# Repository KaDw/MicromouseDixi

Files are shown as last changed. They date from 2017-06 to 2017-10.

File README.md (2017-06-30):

# Micromouse Dixi #
	
|  |  |
| ----- | ----- |
| Width | 79mm  |
| Length  | 95mm  |
| Weight  | |
| Wheels  | 3D printed wheels + MZT301-20 tyres  |
| Microcontroller  | STM32F405RGT6  |
| Gear ratio  | 27:42  |
| Motor  | Pololu 5:1 HPCB  |
| Encoders  | AS55147P  |
| Battery  | Li-Pol Dualsky 7.4V 150mAh 20C  |
| Motor Driver  | TB6612FNG  |
| Sensor | TEFT4300 + SFH4545 X 6  |
| Gyro | MPU6050  |

[BOM](https://docs.google.com/spreadsheets/d/1-OBliDhJaHepW5BqGZAOIfc_tJH4ITr39Bejxq-Zry4/edit?usp=sharing)

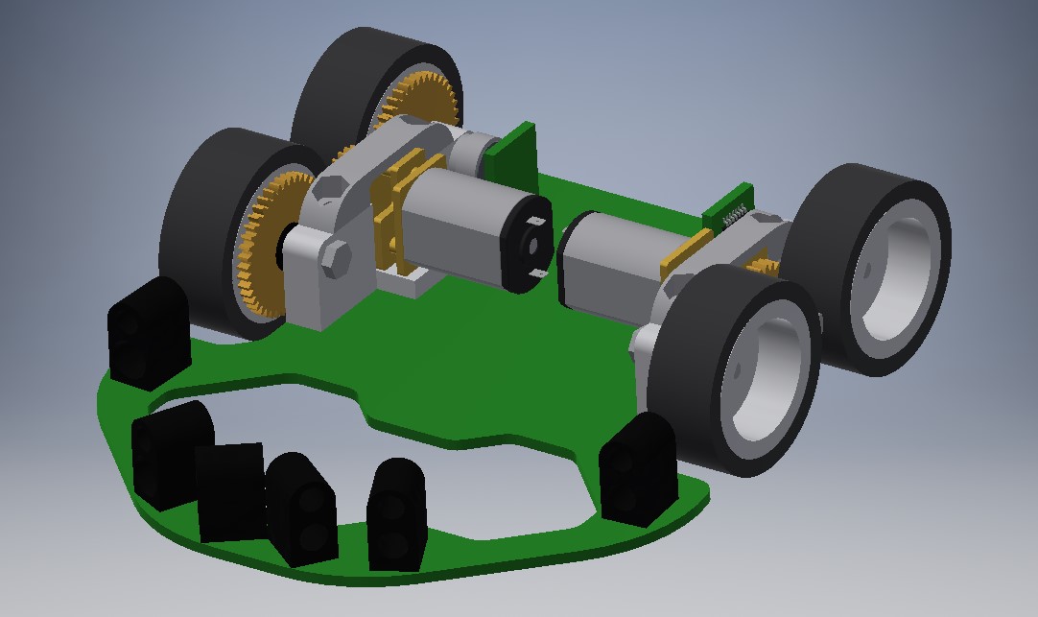
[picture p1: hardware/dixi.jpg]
Dixi


### Development tools ###

* STM32CubeMX Version 4.17.0
* HAL Libraries - FW_F4 V1.13.1
* Keil uVision 5.21a
* EagleCAD 7.7
* Autodesk Inventor 2016

Development tools available [here](https://drive.google.com/open?id=0B6SlddUSFtelRTBFR0EwWk1qT1k)

### Setup ###

* CubeMX setup
You can get HAL libraries by going to Help->Install New Libraries->Firmware Package for Family STM32F4.
...

### Who do I talk to? ###

* Karol Trzciński k.trzcinski95@gmail.com
* Karol Dworakowski karol1dw@gmail.com

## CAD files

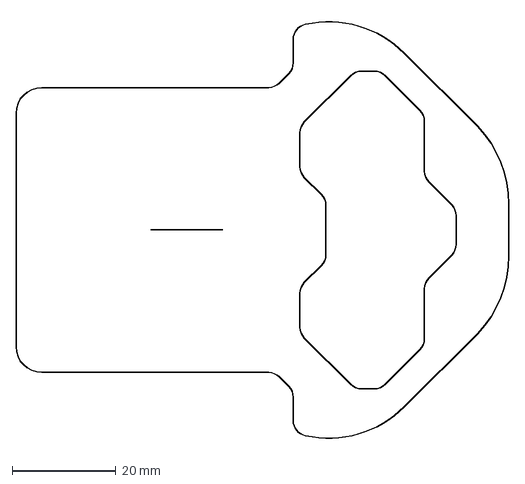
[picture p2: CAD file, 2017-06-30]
hardware/models/mainpcb.dxf
95.2 x 82.5 mm

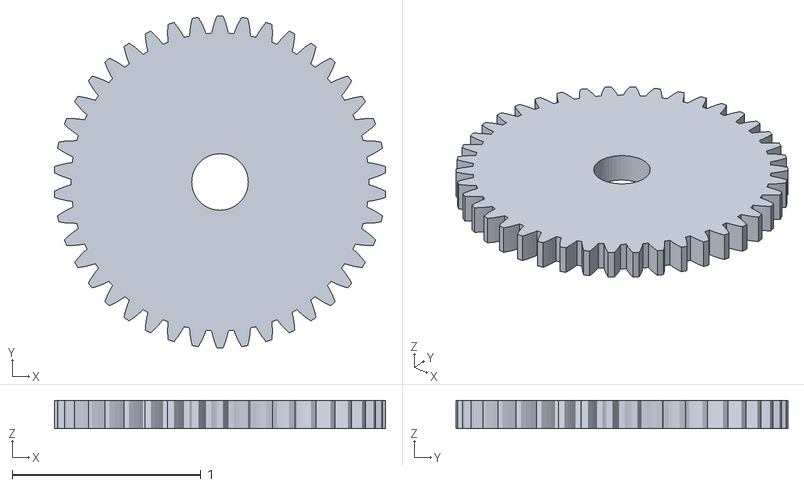
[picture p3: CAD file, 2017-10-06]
hardware/models/gear_42t.stl
1.76 x 1.76 x 0.15

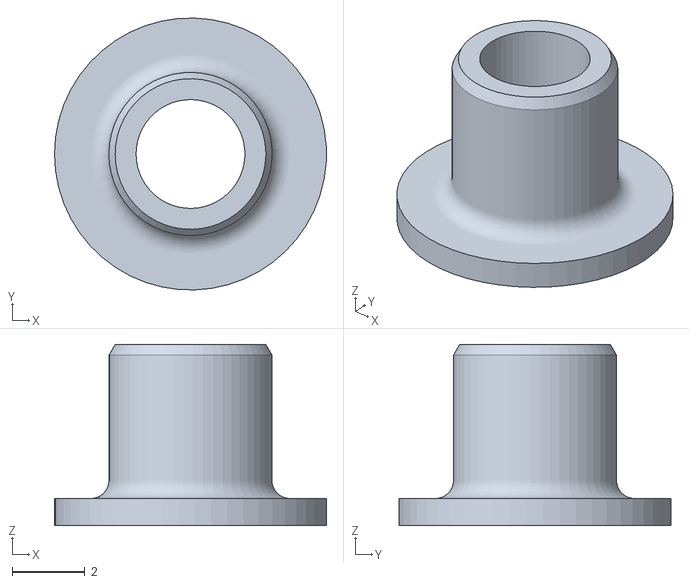
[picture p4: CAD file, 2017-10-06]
hardware/models/XFM_0304_05_2.stl
7.50 x 7.50 x 5.00

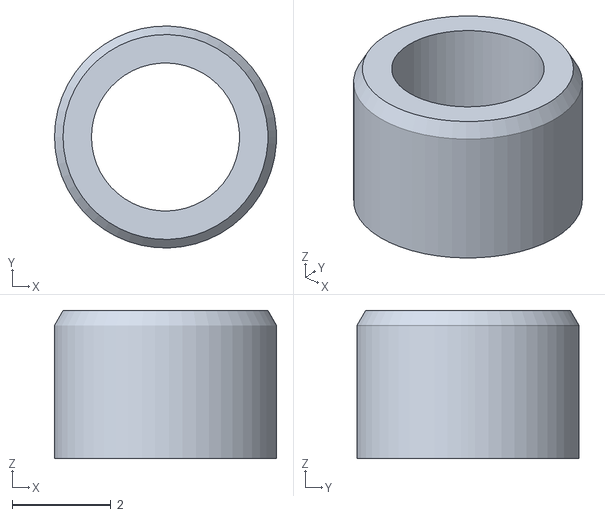
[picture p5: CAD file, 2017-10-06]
hardware/models/XSM_0304_03_1.stl
4.50 x 4.50 x 3.00

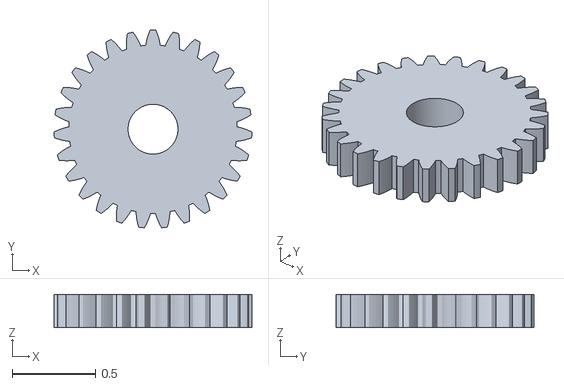
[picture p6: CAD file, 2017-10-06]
hardware/models/gear_27t.stl
1.19 x 1.19 x 0.2

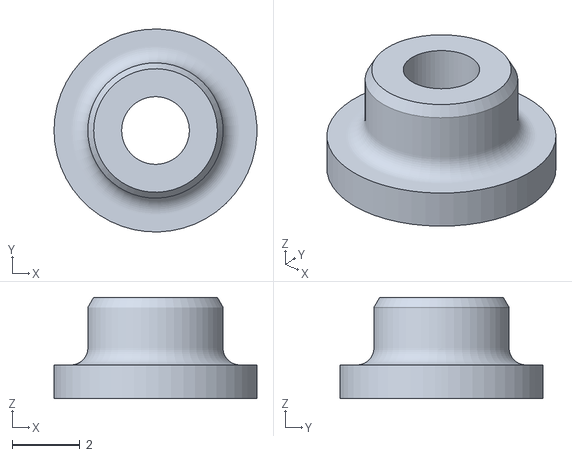
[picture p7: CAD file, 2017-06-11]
hardware/models/XFM_020406_03_2.stl
6.00 x 6.00 x 3.00

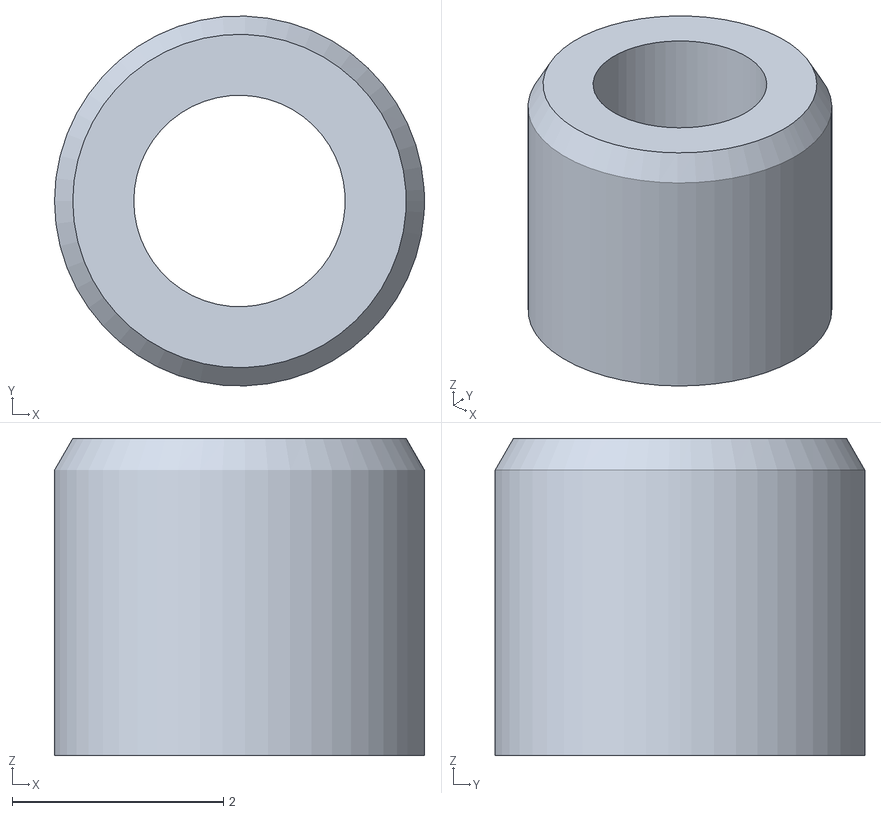
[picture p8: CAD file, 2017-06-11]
hardware/models/XSM_0203_03_1.stl
3.50 x 3.50 x 3.00

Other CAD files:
hardware/models/Dixi.iam
hardware/models/Dixi/Design Accelerator/Spur Gear14.ipt
hardware/models/Dixi/Design Accelerator/Spur Gear23.ipt
hardware/models/Dixi/Design Accelerator/Spur Gears3.iam
hardware/models/Dixi/Design Accelerator/Spur Gears4.iam
hardware/models/XFM_020406_03_233.ipt
hardware/models/XSM_0203_03_1.ipt
hardware/models/bolt.ipt
hardware/models/enc_pcb.ipt
hardware/models/koloz.ipt
hardware/models/led_mount.ipt
hardware/models/magnet.ipt
hardware/models/magnet_holder.ipt
hardware/models/mainpcb.ipt
hardware/models/motor.ipt
hardware/models/togh.ipt
hardware/models/togh_MIR5.ipt
hardware/models/top_mount.ipt
hardware/models/tssop14.iam
hardware/models/tssop14_1.ipt
hardware/models/tssop14_2.ipt
hardware/models/tssop14_3.ipt
hardware/models/tyre.ipt
hardware/models/wheel.ipt

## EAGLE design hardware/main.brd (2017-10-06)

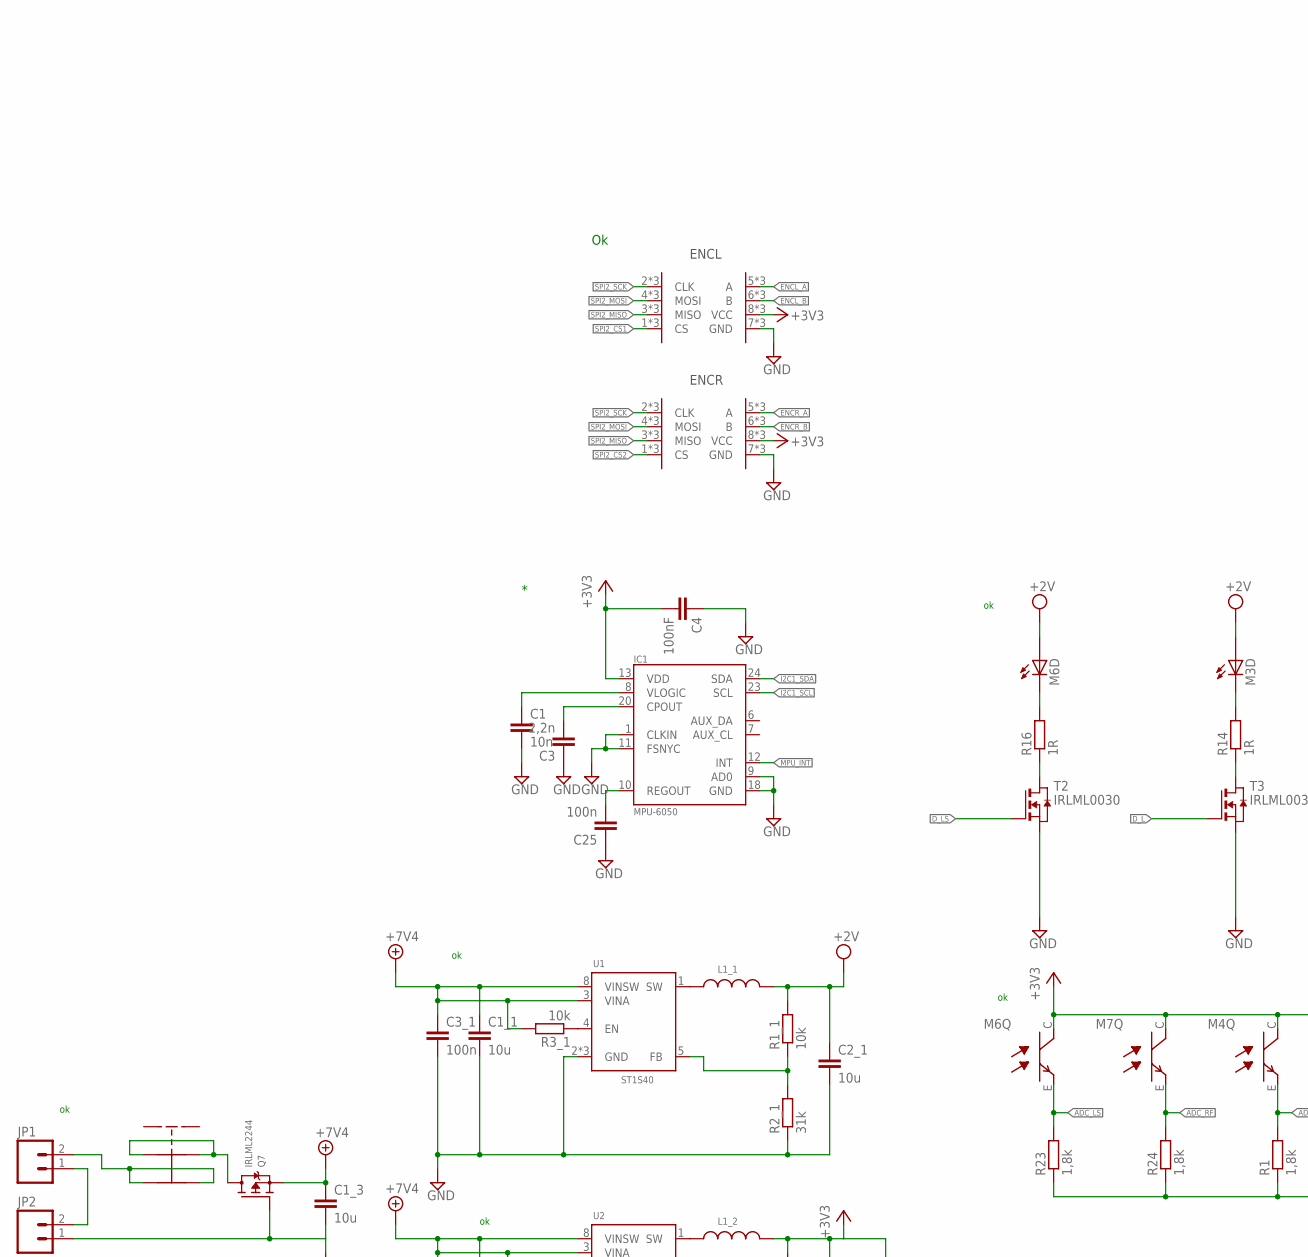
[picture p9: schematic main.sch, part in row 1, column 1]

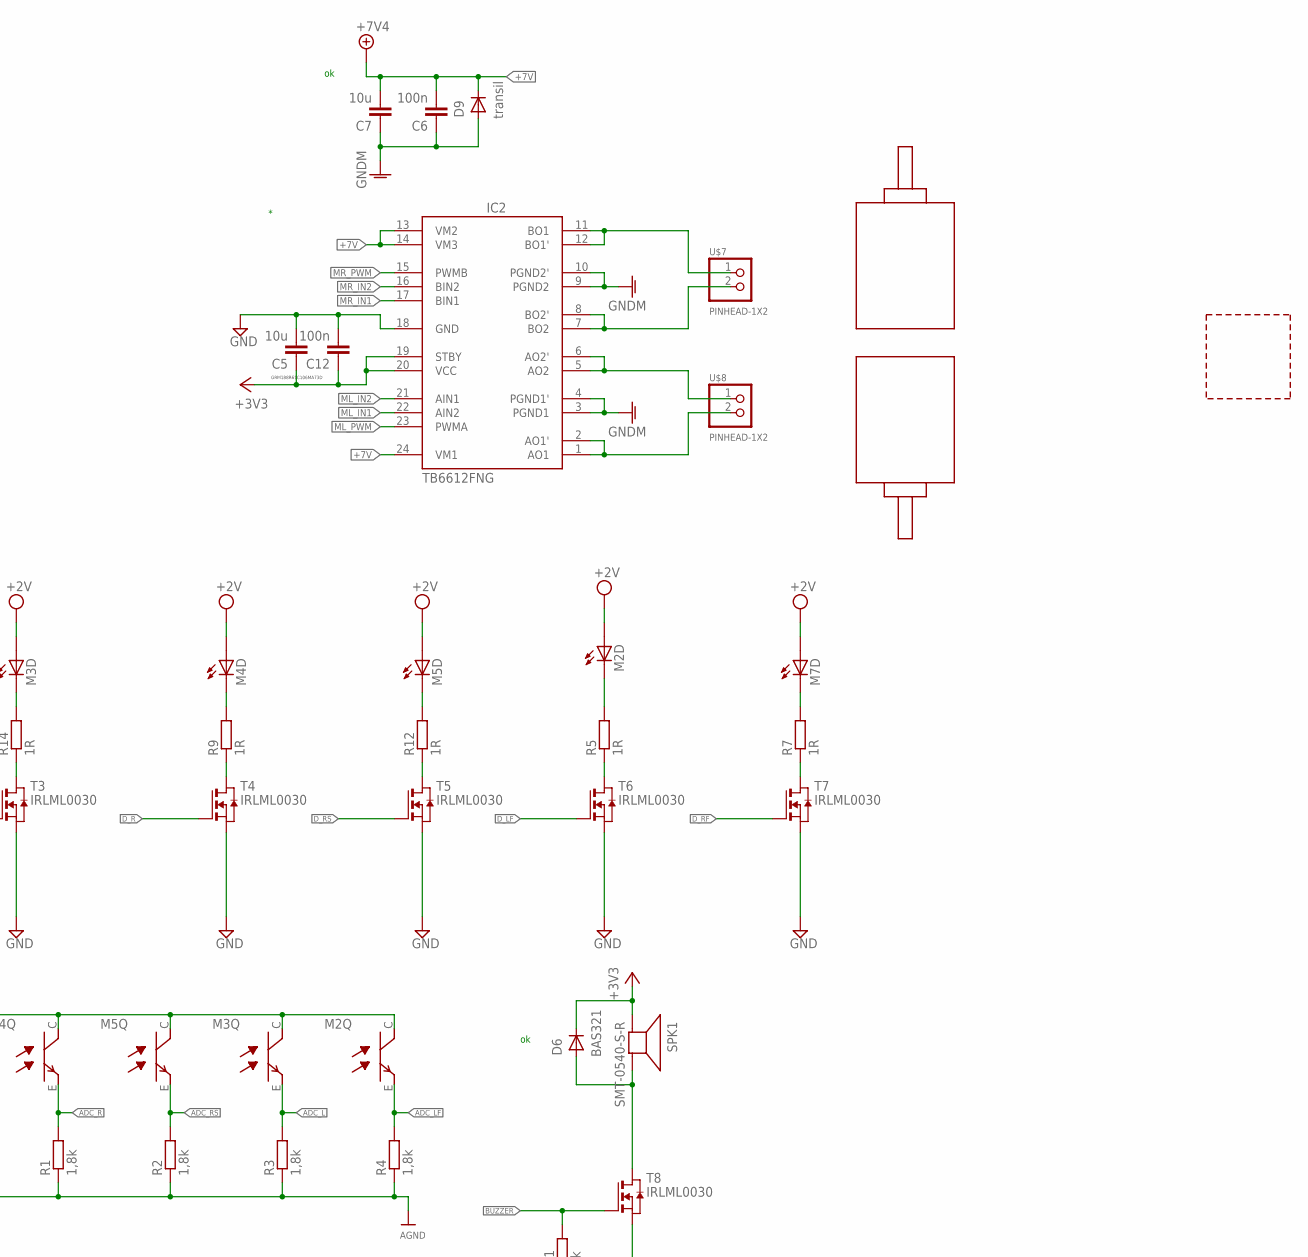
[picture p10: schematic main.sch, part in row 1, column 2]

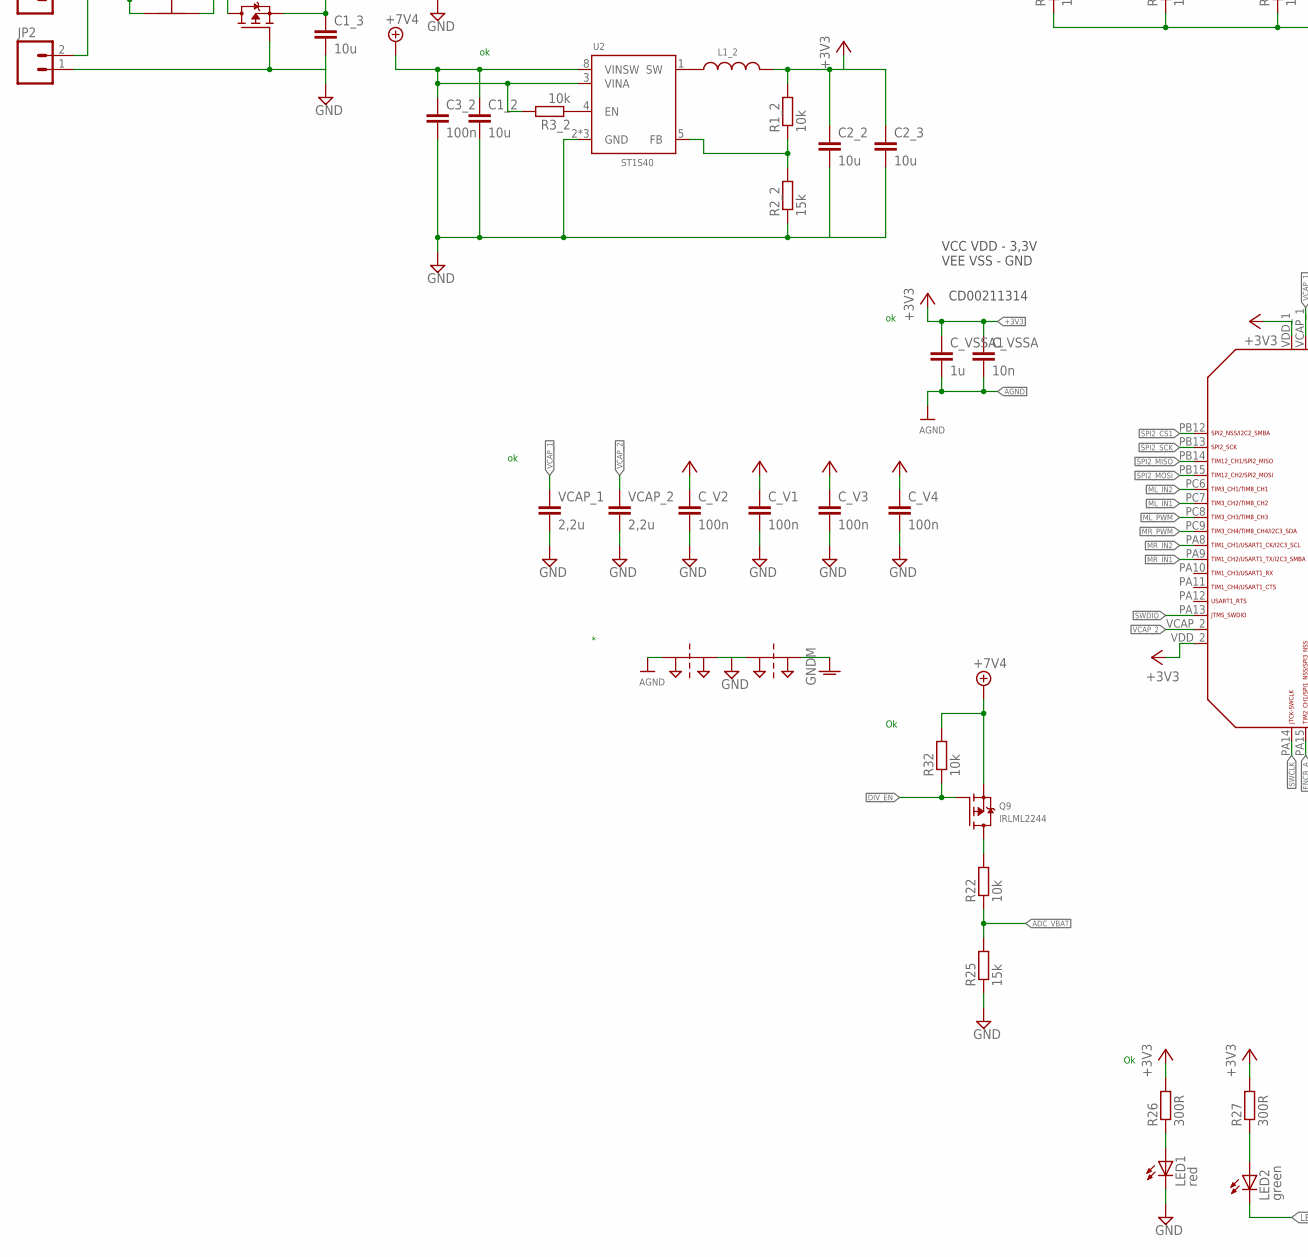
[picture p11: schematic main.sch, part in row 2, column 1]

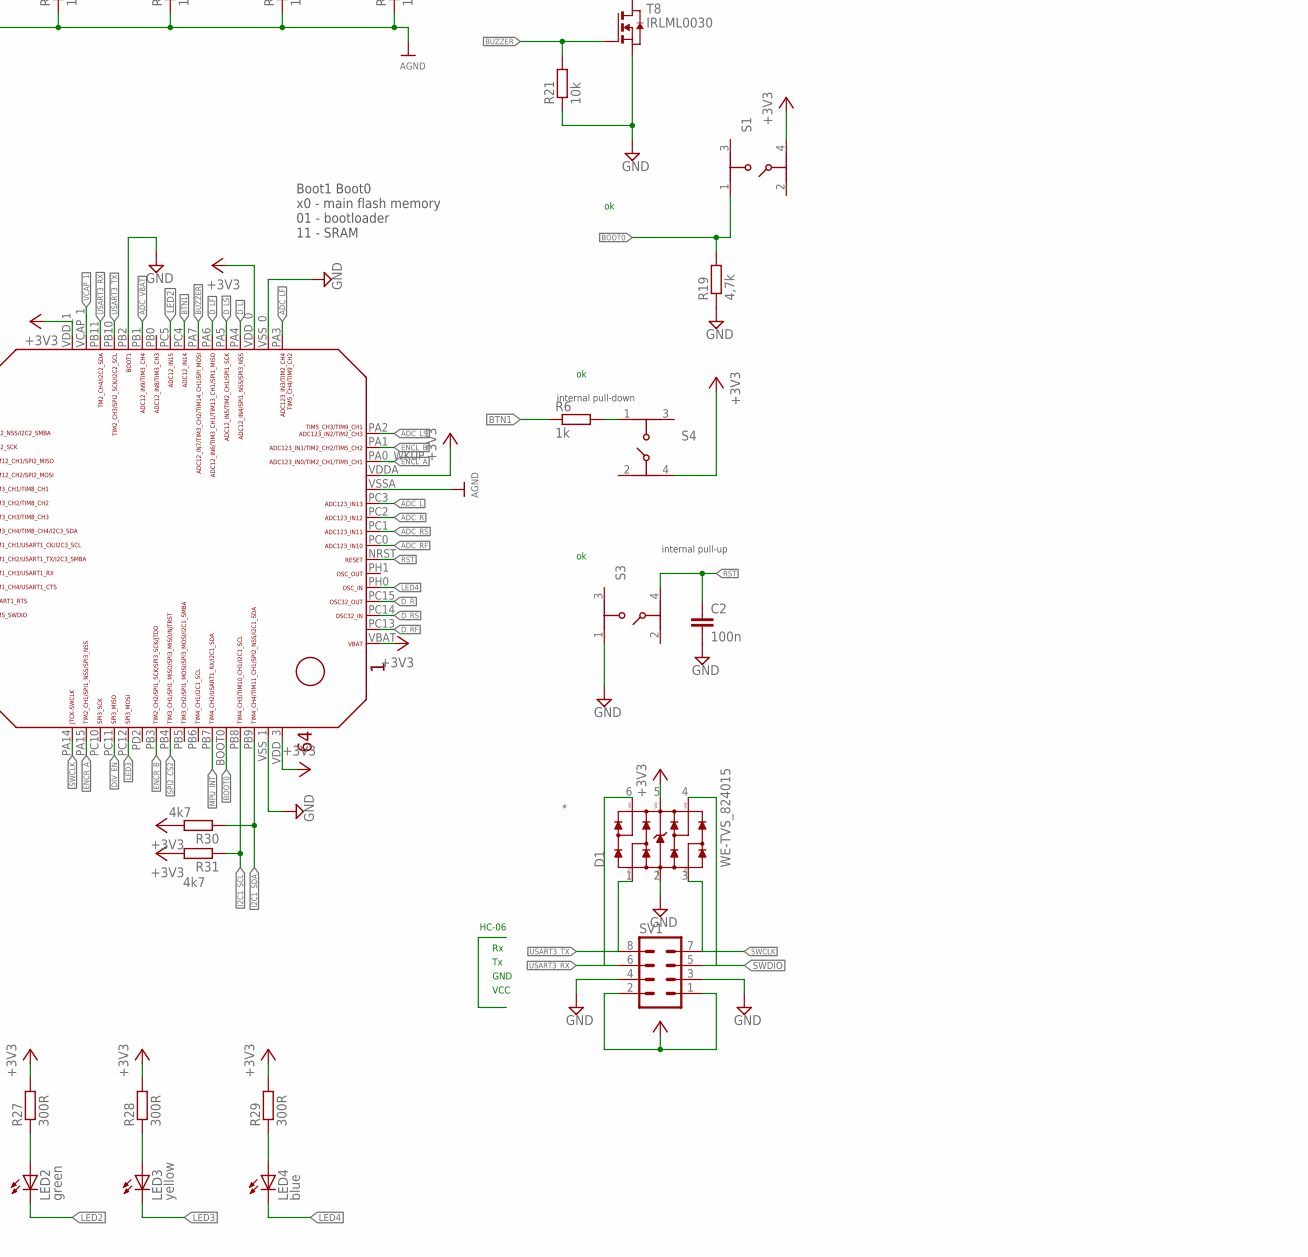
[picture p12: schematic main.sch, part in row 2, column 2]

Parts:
C1: 10n; C0603
C1_1, C1_2, C1_3, C2_1, C2_2, C2_3, C5: 10u; C0805
C2, C3_1, C3_2, C6, C12, C25: 100n; C0603
C3: 2,2n; C0603
C4: 100nF; C0603
C7: 10u; C1206
C_V1, C_V2, C_V3, C_V4: 100n; C0603
C_VSSA: 10n; C0603
C_VSSA1: 1u; C0603
D1: WE-TVS_824015; WE-TVS_SOT23-6L
D6: BAS321; SOD323(F)
D9: transil; SOD323(F)
IC1: MPU-6050; QFN.24.4X4
IC2: TB6612FNG; SSOP24
JP1, JP2: M02POLAR; MOLEX-1X2
L1: LABITYNT; LABIRYNT
L1_1: WE-MAIA_3015_78438335068; WE-MAIA_3015
L1_2: WE-MAIA_3015_78438335033; WE-MAIA_3015
LED1: red; SML1206
LED2: green; SML1206
LED3: yellow; SML1206
LED4: blue; SML1206
M1: MOTOR_MOUNT_V2
M2, M3, M4, M5, M6, M7: LED_MOUNT
ON: PRZELACZNIK_SUWAKOWY
PT1, PT2: 2PT_GND_TIE
Q7, Q9: IRLML2244; SOT23-R
R1, R2, R3, R4, R23, R24: 1,8k; R0603
R1_1, R1_2, R3_1, R3_2, R21, R22, R32: 10k; R0603
R2_1: 31k; R0603
R2_2, R25: 15k; R0603
R5, R7, R9, R12, R14, R16: 1R; R0603
R6: 1k; R0603
R19: 4,7k; R0603
R26, R27, R28, R29: 300R; R0603
R30, R31: 4k7; R0603
S1, S3, S4: 434153017835
SPK1: SMT-0540-S-R
SV1: MA04-2
T2, T3, T4, T5, T6, T7, T8: IRLML0030; SOT-23
U1, U2: ST1S40; SO8
U3: STM32F4X5; STM32F4-LQFP64
U$7, U$8: PINHEAD-1X2; PIHEAD-1X2
U$9, U$10: ENCODER_MOUNT
VCAP_1, VCAP_2: 2,2u; C0603

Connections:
+3V3: C2_2.1, C2_3.1, C4.2, C5.1, C12.1, C_V1.1, C_V2.1, C_V3.1, C_V4.1, C_VSSA.1, C_VSSA1.1, D1.5 (VDD), D6.1 (K), IC1.13 (VDD), IC2.19 (STBY), IC2.20 (VCC), L1_2.2, M2.C, M3.C, M4.C, M5.C, M6.C, M7.C, R1_2.2, R26.2, R27.2, R28.2, R29.2, R30.2, R31.2, S1.4, S4.4, SPK1.- (+), SV1.1, SV1.2, U3.VBAT, U3.VDDA, U3.VDD_0, U3.VDD_1, U3.VDD_2, U3.VDD_3, U$9.8 (VCC), U$9.8_1 (VCC), U$9.8_2 (VCC), U$10.8 (VCC), U$10.8_1 (VCC), U$10.8_2 (VCC)
+7V: C1_1.1, C1_2.1, C1_3.1, C3_1.1, C3_2.1, C6.2, C7.2, D9.1 (K), IC2.13 (VM2), IC2.14 (VM3), IC2.24 (VM1), Q7.2 (S), Q9.2 (S), R3_1.2, R3_2.2, R32.2, U1.3 (VINA), U1.8 (VINSW), U2.3 (VINA), U2.8 (VINSW)
ADC_L: M3.E, R3.2, U3.PC3
ADC_LF: M2.E, R4.2, U3.PA3
ADC_LS: M6.E, R23.2, U3.PA2
ADC_R: M4.E, R1.2, U3.PC2
ADC_RF: M7.E, R24.2, U3.PC0
ADC_RS: M5.E, R2.2, U3.PC1
ADC_VBAT: R22.1, R25.2, U3.PB1
AGND: C_VSSA.2, C_VSSA1.2, PT1.P$1, R1.1, R2.1, R3.1, R4.1, R23.1, R24.1, U3.VSSA
BOOT0: R19.2, S1.1, U3.BOOT0
BTN1: R6.1, U3.PC4
BUZZER: R21.2, T8.3 (G), U3.PA7
DIV_EN: Q9.1 (G), R32.1, U3.PC11
D_L: T3.3 (G), U3.PA4
D_LF: T6.3 (G), U3.PA6
D_LS: T2.3 (G), U3.PA5
D_R: T4.3 (G), U3.PC15
D_RF: T7.3 (G), U3.PC13
D_RS: T5.3 (G), U3.PC14
ENCL_A: U3.PA0_WKUP (PA0_AKUP), U$9.5 (A), U$9.5_1 (A), U$9.5_2 (A)
ENCL_B: U3.PA1, U$9.6 (B), U$9.6_1 (B), U$9.6_2 (B)
ENCR_A: U3.PA15, U$10.5 (A), U$10.5_1 (A), U$10.5_2 (A)
ENCR_B: U3.PB3, U$10.6 (B), U$10.6_1 (B), U$10.6_2 (B)
GND: C1.2, C1_1.2, C1_2.2, C1_3.2, C2.2, C2_1.2, C2_2.2, C2_3.2, C3.1, C3_1.2, C3_2.2, C4.1, C5.2, C12.2, C25.1, C_V1.2, C_V2.2, C_V3.2, C_V4.2, D1.2 (GND), IC1.1 (CLKIN), IC1.9 (AD0), IC1.11 (FSNYC), IC1.18 (GND), IC2.18 (GND), JP2.1, LED1.C, PT1.P$2, PT2.P$1, Q7.1 (G), R2_1.1, R2_2.1, R19.1, R21.1, R25.1, S3.1, SV1.3, SV1.4, T2.2 (S), T3.2 (S), T4.2 (S), T5.2 (S), T6.2 (S), T7.2 (S), T8.2 (S), U1.2 (GND), U1.6 (GND), U1.7 (GND), U2.2 (GND), U2.6 (GND), U2.7 (GND), U3.PB2, U3.VSS_0, U3.VSS_1, U$9.7 (GND), U$9.7_1 (GND), U$9.7_2 (GND), U$10.7 (GND), U$10.7_1 (GND), U$10.7_2 (GND), VCAP_1.2, VCAP_2.2
GNDA: C6.1, C7.1, D9.2 (A), IC2.3 (PGND1), IC2.4 (PGND1'), IC2.9 (PGND2), IC2.10 (PGND2'), PT2.P$2
I2C1_SCL: IC1.23 (SCL), R31.1, U3.PB8
I2C1_SDA: IC1.24 (SDA), R30.1, U3.PB9
LED2: LED2.C, U3.PC5
LED3: LED3.C, U3.PC12
LED4: LED4.C, U3.PH0
ML_IN1: IC2.22 (AIN2), U3.PC7
ML_IN2: IC2.21 (AIN1), U3.PC6
ML_PWM: IC2.23 (PWMA), U3.PC8
MPU_INT: IC1.12 (INT), U3.PB7
MR_IN1: IC2.17 (BIN1), U3.PA9
MR_IN2: IC2.16 (BIN2), U3.PA8
MR_PWM: IC2.15 (PWMB), U3.PC9
unnamed: M7.- (C), R7.2
unnamed: M2.- (C), R5.2
unnamed: R5.1, T6.1 (D)
unnamed: R7.1, T7.1 (D)
unnamed: M4.- (C), R9.2
unnamed: R9.1, T4.1 (D)
unnamed: M5.- (C), R12.2
unnamed: R12.1, T5.1 (D)
unnamed: M3.- (C), R14.2
unnamed: R14.1, T3.1 (D)
unnamed: M6.- (C), R16.2
unnamed: R16.1, T2.1 (D)
unnamed: Q9.3 (D), R22.2
unnamed: L1_1.1, U1.1 (SW)
unnamed: L1_2.1, U2.1 (SW)
unnamed: R3_1.1, U1.4 (EN)
unnamed: R3_2.1, U2.4 (EN)
unnamed: JP1.1, JP2.2
unnamed: LED1.A, R26.1
unnamed: LED2.A, R27.1
unnamed: LED3.A, R28.1
unnamed: LED4.A, R29.1
unnamed: R6.2, S4.1
unnamed: C25.2, IC1.10 (REGOUT)
unnamed: D6.2 (A), SPK1.+ (-), T8.1 (D)
unnamed: C3.2, IC1.20 (CPOUT)
unnamed: C1.1, IC1.8 (VLOGIC)
unnamed: IC2.1 (AO1), IC2.2 (AO1'), U$8.2
unnamed: IC2.11 (BO1), IC2.12 (BO1'), U$7.1
unnamed: IC2.7 (BO2), IC2.8 (BO2'), U$7.2
unnamed: IC2.5 (AO2), IC2.6 (AO2'), U$8.1
unnamed: ON.2, ON.5, Q7.3 (D)
unnamed: JP1.2, ON.3, ON.6
unnamed: R1_2.1, R2_2.2, U2.5 (FB)
unnamed: R1_1.1, R2_1.2, U1.5 (FB)
RST: C2.1, S3.4, U3.NRST
SPI2_CS1: U3.PB12, U$9.1 (CS), U$9.1_1 (CS), U$9.1_2 (CS)
SPI2_CS2: U3.PB4, U$10.1 (CS), U$10.1_1 (CS), U$10.1_2 (CS)
SPI2_MISO: U3.PB14, U$9.3 (MISO), U$9.3_1 (MISO), U$9.3_2 (MISO), U$10.3 (MISO), U$10.3_1 (MISO), U$10.3_2 (MISO)
SPI2_MOSI: U3.PB15, U$9.4 (MOSI), U$9.4_1 (MOSI), U$9.4_2 (MOSI), U$10.4 (MOSI), U$10.4_1 (MOSI), U$10.4_2 (MOSI)
SPI2_SCK: U3.PB13, U$9.2 (CLK), U$9.2_1 (CLK), U$9.2_2 (CLK), U$10.2 (CLK), U$10.2_1 (CLK), U$10.2_2 (CLK)
SWCLK: D1.3, SV1.7, U3.PA14
SWDIO: D1.4, SV1.5, U3.PA13
USART3_RX: D1.6, SV1.6, U3.PB11
USART3_TX: D1.1, SV1.8, U3.PB10
VCAP_1: U3.VCAP_1, VCAP_1.1
VCAP_2: U3.VCAP_2, VCAP_2.1
VCC: C2_1.1, L1_1.2, M2.+ (A), M3.+ (A), M4.+ (A), M5.+ (A), M6.+ (A), M7.+ (A), R1_1.2

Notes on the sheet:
Boot1 Boot0 x0 - main flash memory 01 - bootloader 11 - SRAM
VCC VDD - 3,3V VEE VSS - GND
internal pull-up
internal pull-down
GND
VCC
HC-06
ENCR
ENCL
CD00211314
GRM188R61C106MA73D

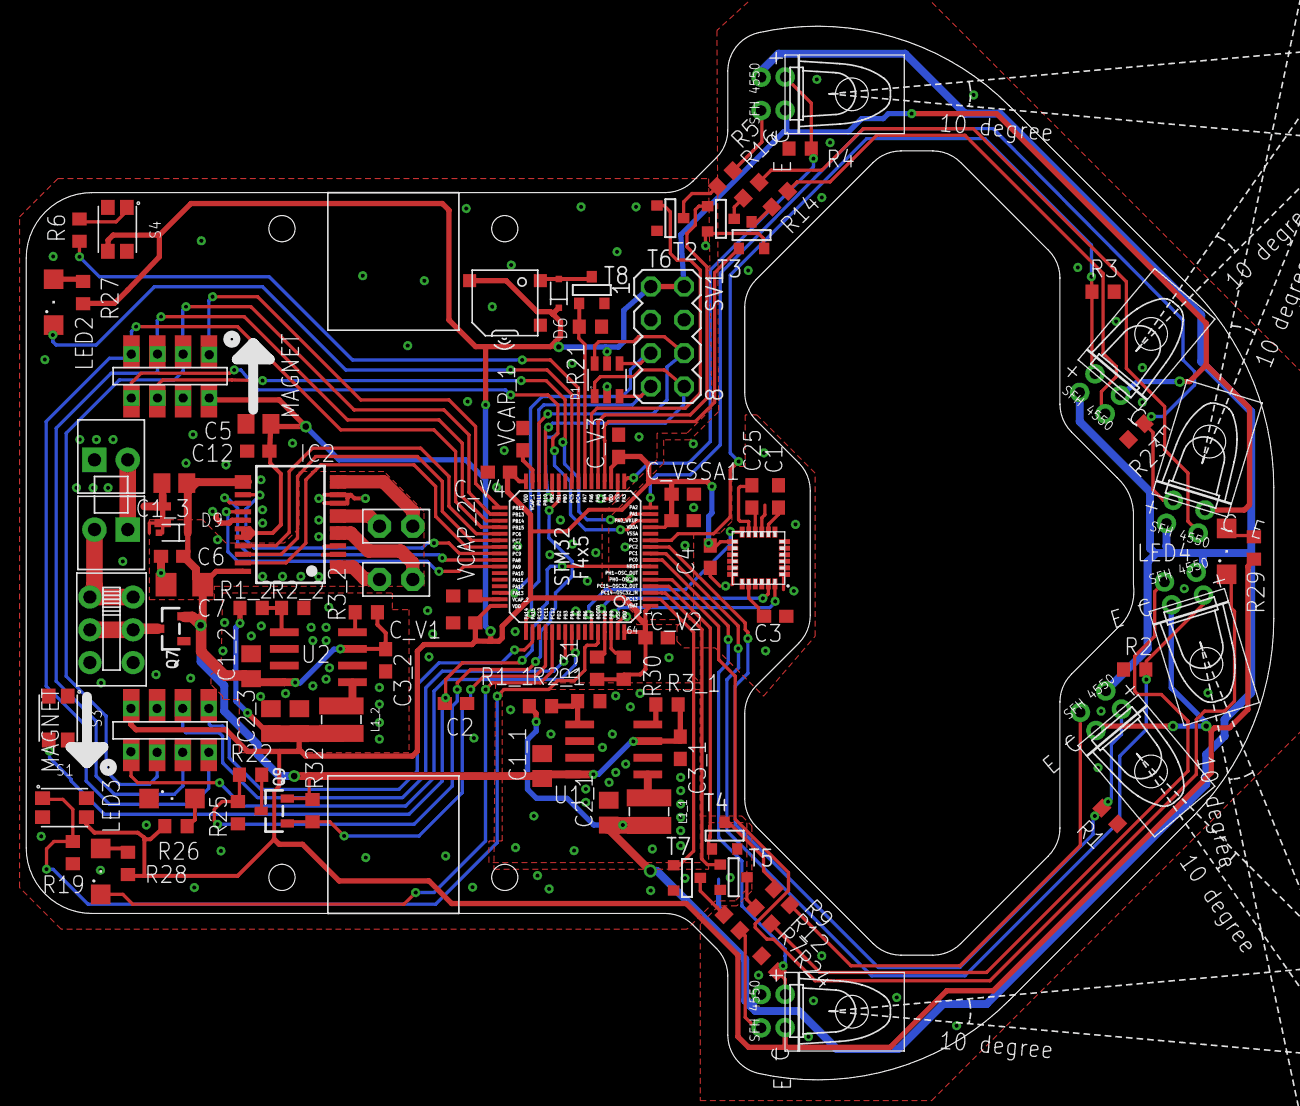
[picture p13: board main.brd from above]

Board: 2 copper layers, 95.2 x 80.4 mm, 100 parts (1 on the bottom side), 86 nets.

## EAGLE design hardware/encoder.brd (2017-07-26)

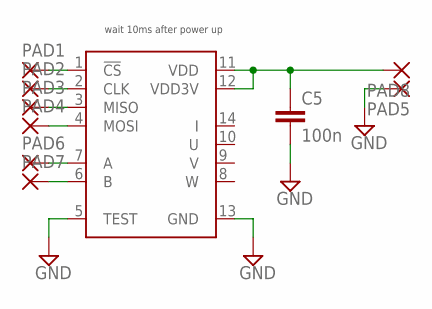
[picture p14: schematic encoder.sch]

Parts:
C5: 100n; C0603
PAD1, PAD2, PAD3, PAD4, PAD5, PAD6, PAD7, PAD8: SMD2; SMD1,27-2,54
U$1: AS5147P; TSSOP-14

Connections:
A: PAD6.1, U$1.7 (A)
B: PAD7.1, U$1.6 (B)
CLK: PAD2.1, U$1.2 (CLK)
CS: PAD1.1, U$1.1 (!CS)
GND: C5.2, PAD5.1, U$1.5 (TEST), U$1.13 (GND)
MISO: PAD3.1, U$1.3 (MISO)
MOSI: PAD4.1, U$1.4 (MOSI)
VCC: C5.1, PAD8.1, U$1.11 (VDD), U$1.12 (VDD3V)

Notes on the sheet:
wait 10ms after power up

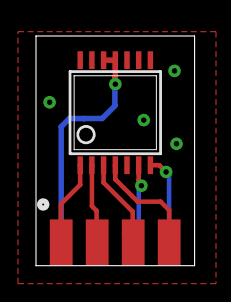
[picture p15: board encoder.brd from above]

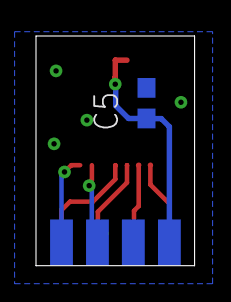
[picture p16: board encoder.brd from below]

Board: 2 copper layers, 8.8 x 12.8 mm, 10 parts (5 on the bottom side), 8 nets.

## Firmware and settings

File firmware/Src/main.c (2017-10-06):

/**
  ******************************************************************************
  * File Name          : main.c
  * Description        : Main program body
  ******************************************************************************
  ** This notice applies to any and all portions of this file
  * that are not between comment pairs USER CODE BEGIN and
  * USER CODE END. Other portions of this file, whether 
  * inserted by the user or by software development tools
  * are owned by their respective copyright owners.
  *
  * COPYRIGHT(c) 2017 STMicroelectronics
  *
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
  ******************************************************************************
  */
/* Includes ------------------------------------------------------------------*/
#include "main.h"
#include "stm32f4xx_hal.h"
#include "adc.h"
#include "dma.h"
#include "i2c.h"
#include "spi.h"
#include "tim.h"
#include "usart.h"
#include "gpio.h"

/* USER CODE BEGIN Includes */
#include "port/as5147p.h"
#include "port/mpu6050.h"
#include "utils/logger.h"

/* USER CODE END Includes */


/* USER CODE BEGIN PV */

/* USER CODE END PV */

void SystemClock_Config(void);

/* USER CODE BEGIN PFP */

/* USER CODE END PFP */

/* USER CODE BEGIN 0 */
float test[6];
/* USER CODE END 0 */

int main(void)
{

  /* USER CODE BEGIN 1 */
	logger_init();

  /* USER CODE END 1 */

  /* MCU Configuration----------------------------------------------------------*/

  /* Reset of all peripherals, Initializes the Flash interface and the Systick. */
  HAL_Init();

  /* Configure the system clock */
  SystemClock_Config();

  /* Initialize all configured peripherals */
  MX_GPIO_Init();
  MX_DMA_Init();
  MX_ADC1_Init();
  MX_TIM6_Init();
  MX_TIM2_Init();
  MX_TIM5_Init();
  MX_I2C1_Init();
  MX_SPI2_Init();
  MX_TIM3_Init();
  MX_USART3_UART_Init();

  /* USER CODE BEGIN 2 */

  if(mpu_selftest())
	  while(1);
  /* USER CODE END 2 */

  /* Infinite loop */
  /* USER CODE BEGIN WHILE */
  while (1)
  {
  /* USER CODE END WHILE */

  /* USER CODE BEGIN 3 */
	  HAL_GPIO_TogglePin(LED2_GPIO_Port, LED2_Pin);
	  HAL_Delay(100);

  }
  /* USER CODE END 3 */

}

/** System Clock Configuration
*/
void SystemClock_Config(void)
{

  RCC_OscInitTypeDef RCC_OscInitStruct;
  RCC_ClkInitTypeDef RCC_ClkInitStruct;

    /**Configure the main internal regulator output voltage 
    */
  __HAL_RCC_PWR_CLK_ENABLE();

  __HAL_PWR_VOLTAGESCALING_CONFIG(PWR_REGULATOR_VOLTAGE_SCALE1);

    /**Initializes the CPU, AHB and APB busses clocks 
    */
  RCC_OscInitStruct.OscillatorType = RCC_OSCILLATORTYPE_HSI;
  RCC_OscInitStruct.HSIState = RCC_HSI_ON;
  RCC_OscInitStruct.HSICalibrationValue = 16;
  RCC_OscInitStruct.PLL.PLLState = RCC_PLL_ON;
  RCC_OscInitStruct.PLL.PLLSource = RCC_PLLSOURCE_HSI;
  RCC_OscInitStruct.PLL.PLLM = 8;
  RCC_OscInitStruct.PLL.PLLN = 168;
  RCC_OscInitStruct.PLL.PLLP = RCC_PLLP_DIV2;
  RCC_OscInitStruct.PLL.PLLQ = 4;
  if (HAL_RCC_OscConfig(&RCC_OscInitStruct) != HAL_OK)
  {
    _Error_Handler(__FILE__, __LINE__);
  }

    /**Initializes the CPU, AHB and APB busses clocks 
    */
  RCC_ClkInitStruct.ClockType = RCC_CLOCKTYPE_HCLK|RCC_CLOCKTYPE_SYSCLK
                              |RCC_CLOCKTYPE_PCLK1|RCC_CLOCKTYPE_PCLK2;
  RCC_ClkInitStruct.SYSCLKSource = RCC_SYSCLKSOURCE_PLLCLK;
  RCC_ClkInitStruct.AHBCLKDivider = RCC_SYSCLK_DIV1;
  RCC_ClkInitStruct.APB1CLKDivider = RCC_HCLK_DIV4;
  RCC_ClkInitStruct.APB2CLKDivider = RCC_HCLK_DIV2;

  if (HAL_RCC_ClockConfig(&RCC_ClkInitStruct, FLASH_LATENCY_5) != HAL_OK)
  {
    _Error_Handler(__FILE__, __LINE__);
  }

    /**Configure the Systick interrupt time 
    */
  HAL_SYSTICK_Config(HAL_RCC_GetHCLKFreq()/1000);

    /**Configure the Systick 
    */
  HAL_SYSTICK_CLKSourceConfig(SYSTICK_CLKSOURCE_HCLK);

  /* SysTick_IRQn interrupt configuration */
  HAL_NVIC_SetPriority(SysTick_IRQn, 0, 0);
}

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


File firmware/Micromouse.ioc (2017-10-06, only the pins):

Mcu.UserName=STM32F405RGTx
PA0-WKUP.GPIO_Label=ENCL_A
PA0-WKUP.Signal=S_TIM5_CH1
PA1.GPIO_Label=ENCL_B
PA1.Signal=S_TIM5_CH2
PA13.Signal=SYS_JTMS-SWDIO
PA14.Signal=SYS_JTCK-SWCLK
PA15.GPIO_Label=ENCR_A
PA15.Signal=S_TIM2_CH1_ETR
PA2.GPIO_Label=ADC_LS
PA2.Signal=ADCx_IN2
PA3.GPIO_Label=ADC_LF
PA3.Signal=ADCx_IN3
PA4.GPIO_Label=D_L
PA4.Signal=GPIO_Output
PA5.GPIO_Label=D_LS
PA5.Signal=GPIO_Output
PA6.GPIO_Label=D_LF
PA6.Signal=GPIO_Output
PA7.GPIO_Label=BUZZER
PA7.Signal=GPIO_Output
PA8.GPIO_Label=MR_IN2
PA8.Signal=GPIO_Output
PA9.GPIO_Label=MR_IN1
PA9.Signal=GPIO_Output
PB1.GPIO_Label=ADC_VBAT
PB1.Signal=ADCx_IN9
PB10.Signal=USART3_TX
PB11.Signal=USART3_RX
PB12.GPIO_Label=SPI2_CS1
PB12.Signal=GPIO_Output
PB13.Signal=SPI2_SCK
PB14.Signal=SPI2_MISO
PB15.Signal=SPI2_MOSI
PB3.GPIO_Label=ENCR_B
PB3.Signal=S_TIM2_CH2
PB4.GPIO_Label=SPI2_CS2
PB4.Signal=GPIO_Output
PB6.Signal=GPIO_Input
PB7.Signal=GPIO_Input
PB8.Signal=I2C1_SCL
PB9.Signal=I2C1_SDA
PC0.GPIO_Label=ADC_RS
PC0.Signal=ADCx_IN10
PC1.GPIO_Label=ADC_RF
PC1.Signal=ADCx_IN11
PC11.GPIO_Label=DIV_EN
PC11.Signal=GPIO_Output
PC12.GPIO_Label=LED3
PC12.Signal=GPIO_Output
PC13-ANTI_TAMP.GPIO_Label=D_RF
PC13-ANTI_TAMP.Signal=GPIO_Output
PC14-OSC32_IN.GPIO_Label=D_RS
PC14-OSC32_IN.Signal=GPIO_Output
PC15-OSC32_OUT.GPIO_Label=D_R
PC15-OSC32_OUT.Signal=GPIO_Output
PC2.GPIO_Label=ADC_R
PC2.Signal=ADCx_IN12
PC3.GPIO_Label=ADC_L
PC3.Signal=ADCx_IN13
PC4.GPIO_Label=BTN1
PC4.Signal=GPIO_Input
PC5.GPIO_Label=LED2
PC5.Signal=GPIO_Output
PC6.GPIO_Label=ML_IN1
PC6.Signal=GPIO_Output
PC7.GPIO_Label=ML_IN2
PC7.Signal=GPIO_Output
PC8.GPIO_Label=ML_PWM
PC8.Signal=S_TIM3_CH3
PC9.GPIO_Label=MR_PWM
PC9.Signal=S_TIM3_CH4
PH0-OSC_IN.GPIO_Label=LED4
PH0-OSC_IN.Signal=GPIO_Output

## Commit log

2017-05-29 initial commit, first 3d model
    [Assembly2.0005.iam, Dixi.iam, bolt.0004.ipt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]
2017-06-04 added sch
    [Dixi.0007.iam, Dixi.iam, bolt.0004.ipt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]
2017-06-07 cleanup, 3d top mount
    [Dixi.0007.iam, Dixi.0010.iam, Dixi.iam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]
2017-06-07 encoder brd
    [encoder.brd, encoder.sch, main.sch]
2017-06-11 fixed 3d model
    [Dixi.0010.iam, Dixi.0015.iam, Dixi.iam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]
2017-06-24 added led_mount to model, pcb elemets grouped
    [Dixi.0033.iam, Dixi.0035.iam, Dixi.iam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]
2017-06-26 power supply layout almost done
    [main.brd, main.sch, togh.0022.ipt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]
2017-06-29 pcb 29.06
    [Dixi.0035.iam, Dixi.0037.iam, Dixi.iam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]
2017-06-29 pcb 29.06 1
    [main.brd, main.sch]
2017-06-29 pcb todo front layout
    [main.brd, main.sch]
2017-06-29 led mount fix
    [main.brd, main.sch]
2017-06-29 Rozmieszczone diody na dziobie, przelotki przy DCDC
    [main.brd, main.sch]
2017-06-30 3d model - v1, gnd plane fun
    [Dixi.0037.iam, Dixi.0038.iam, Dixi.iam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]
2017-06-30 almost done, gnd mess
    [main.brd]
2017-07-01 led resistors changed to 0603, fixed gnd plane
    [main.brd, main.sch]
2017-07-01 polygons fix
    [main.brd, main.sch]
2017-07-02 porzadek z polygonami
    [main.brd]
2017-07-02 dodanie lini od przerwania od MPU, dodanie C na DCDC 3V3, laczenie GNDA GND i GNDM, dodanie diod ESD na programator, rewizja
    [main.brd, main.sch]
2017-07-03 encoder lbr fix, connected gnd
    [main.brd, main.sch]
2017-07-04 bugfix: mosfet przy zasilaniu
    [main.brd, main.sch]
2017-07-04 poprawa 1 sciezki przy bateii
    [main.brd]
2017-07-05 dodanie napisow, odsuniecie kilku sciezek od krawedzi plytki, minimlne zmniejszenie otworu z przodu (aby nie bylo problemu z odlegloscia od krawedzi)
    [main.brd]
2017-07-26 poukladanie warstwy opisowej, dodanie przelotek - wersja finalna
    [encoder.brd, main.brd, main.sch]
2017-08-27 changed wheel shaft size to 3mm
    [Dixi.0038.iam, Dixi.0040.iam, Dixi.iam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]
2017-09-14 dodanie wartosci elementow
    [main.brd, main.sch]
2017-09-18 cleanup, .gitignore fixed
    [Assembly2.0005.iam, Dixi.0040.iam, Spur Gear14.0003.ipt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]
2017-09-21 as5147p spi_read working (ugly code)
    [Micromouse Debug.cfg]
2017-10-06 returns fixed, gyro using dma
    [Micromouse.ioc, as5147p.c, main.c]

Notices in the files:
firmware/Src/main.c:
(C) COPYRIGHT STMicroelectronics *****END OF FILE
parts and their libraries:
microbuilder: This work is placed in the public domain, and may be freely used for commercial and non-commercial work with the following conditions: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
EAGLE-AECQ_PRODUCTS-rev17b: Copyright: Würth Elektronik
